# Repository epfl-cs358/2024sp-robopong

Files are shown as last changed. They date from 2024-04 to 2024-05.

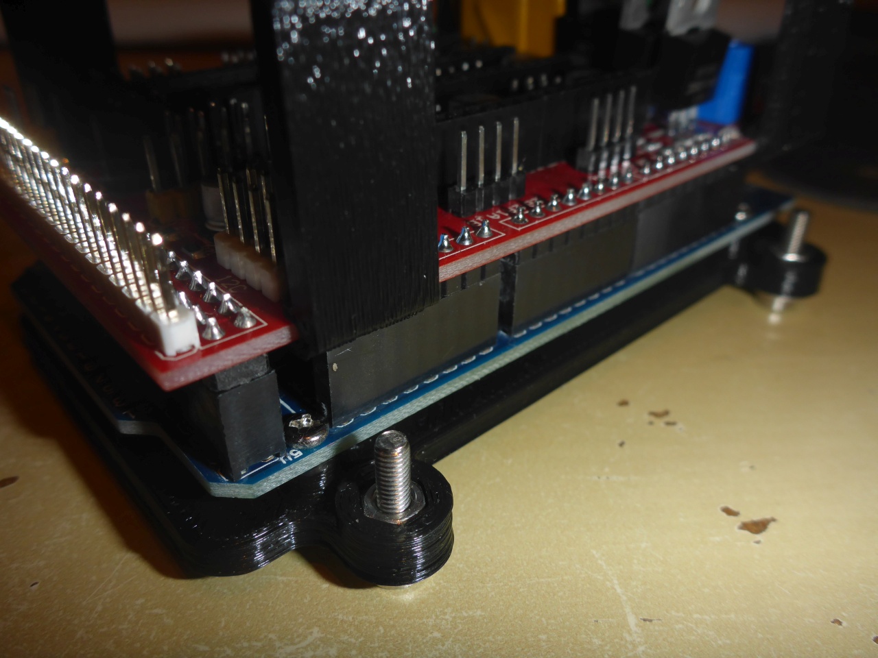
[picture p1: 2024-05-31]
cad/periphery/mega mount/images/P1020768.JPG

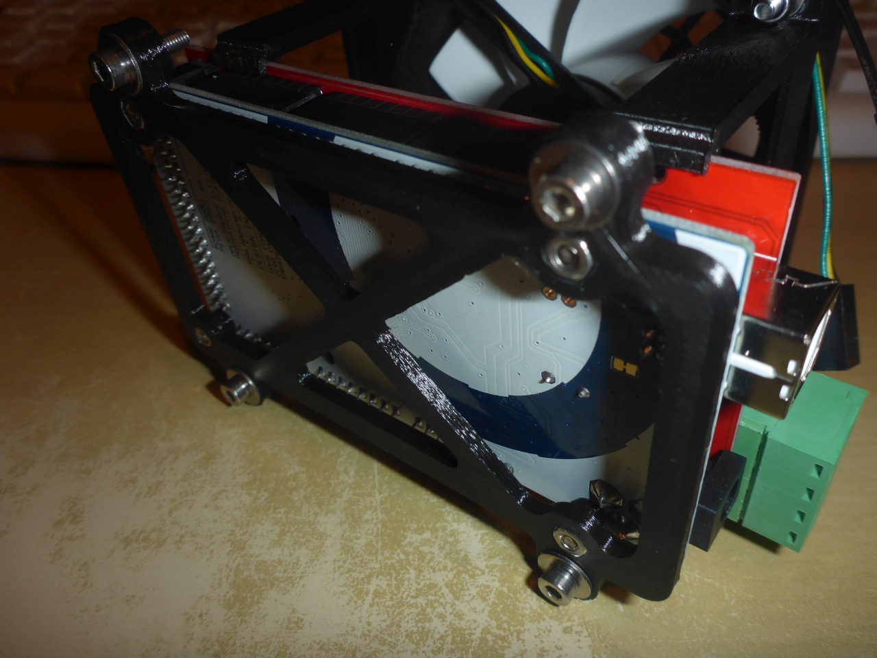
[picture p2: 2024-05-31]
cad/periphery/mega mount/images/P1020765.JPG

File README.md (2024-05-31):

## Robopong

The core concept of our project is a physical version of the classic Pong arcade game, where users bounce a ball back and forth with paddles while attempting to score goals by hitting the ball past the opposing player's paddle. Along with the regular two-player mode, we integrated computer vision into our project, providing the option of single player against a computer opponent, or a completely automated game.





### Authors
- [Amene Gafsi](https://github.com/Amene-Gafsi)
- [Connor Grant](https://github.com/cgrant0)
- [Célien Müller](https://github.com/cemuelle)
- [Jonathan Shu](https://github.com/jonathanshu87)
- [Andrew Yatzkan](https://github.com/AndrewYatzkan)

## BOM
- 2x b-g431b-esc1 motor driver
- 2x br3536 1200kv brushless motor
- 2x AS5600 magnetic encoder
- Arduino Mega
- 12V power supply
- 2x slide potentiometers
- LCD 16x2 screen
- I2C converter
- Webcam Logitech C270
- 2x buttons with LED
- 2x bearings for supporting the motor
- 4x linear bearings
- 4x 8mm by 40cm metal rails
- Belt
- MDF
- Velcro
- Metal rod for camera

## Wiring
### Motors drivers
#### Encoder
326759916-8e4414b6-f468-42d3-b0b5-9535e6a64daa [Schematic from](https://hackaday.io/project/177578-b-g431b-esc-brushless-servo-controller/log/190978-encoders)

To connect the AS5600 encoder to the B-G431B-ESC1 motor drivers, we need to make the following connection :

         +--------------------+       +----------------------+
         |  B-G431B-ESC1      |       |      AS5600          |
         |                    |       |                      |
         |     Z (SCL)     <--+-------+--> SCL               |
         |     B (SDA)     <--+-------+--> SDA               |
         |          5V     <--+-------+--> VCC               |
         |         GND     <--+-------+--> GND               |
         +--------------------+       +----------------------+
The pins on the AS5600 are well labeled
#### Arduino
To control the driver with an Arduino with Serial, we will need to use the RX/TX ports. We will also connect GND in order to have a shared ground and on one of the two drivers will be connect the 5V to the VIN of the Arduino in order to power the arduino.
326795159-361b4c3e-4f68-4188-b18f-7fbf75081d51 [Schematic from](https://www.st.com/resource/en/user_manual/um2516-electronic-speed-controller-discovery-kit-for-drones-with-stm32g431cb-stmicroelectronics.pdf)

         +--------------------+       +----------------------+
         |  B-G431B-ESC1      |       |     Arduino          |
         |  motor 0           |       |                      | 
         |                    |       |                      |
         |          GND    <--+-------+--> GND               |
         |           5V    <--+-------+--> 5V                |
         |           TX    <--+-------+--> RX (Pin 8)        |
         |           RX    <--+-------+--> TX (Pin 9)        |
         +--------------------+       +----------------------+

         +--------------------+       +----------------------+
         |  B-G431B-ESC1      |       |     Arduino          |
         |  motor 1           |       |                      | 
         |                    |       |                      |
         |          GND    <--+-------+--> GND               |
         |           TX    <--+-------+--> RX (Pin 10)       |
         |           RX    <--+-------+--> TX (Pin 11)       |
         +--------------------+       +----------------------+
#### Power and motor
326795266-6a96b532-8359-4901-882d-a318c4af6d5f [Schematic from](https://www.st.com/resource/en/user_manual/um2516-electronic-speed-controller-discovery-kit-for-drones-with-stm32g431cb-stmicroelectronics.pdf)
To power the drivers, we connect respectively the V- and the V+ to the ground and the 12V of our powersupply.
In our system, we are using some XT-60 connectors, on this connectors the flat side is the ground and the other with a sort of triangle is the +. Additionnaly we connect the female side to the power source.
To be able to connect a single power source to the two motor drivers, we make a Y cable.

To connect the motor to the driver, we solder 3 cables to the 3 big pads on the OUTPUT side.

### Potentiometers
To control the motors manually, we need to connect two potentiometers to the Arduino. Both potentiometers send output through the analog pins. We use the following connection (the potentiometer pins are labeled 1-3):

         +------------------------+       +----------------------+
         |  Slide potentiometer 0 |       |       Arduino        |
         |                        |       |                      | 
         |                        |       |                      |
         |          1          <--+-------+-->      GND          |
         |          2          <--+-------+-->      A0           |
         |          3          <--+-------+-->      5V           |
         +------------------------+       +----------------------+

         +------------------------+       +----------------------+
         |  Slide potentiometer 1 |       |       Arduino        |
         |                        |       |                      | 
         |                        |       |                      |
         |          1          <--+-------+-->      GND          |
         |          2          <--+-------+-->      A1           |
         |          3          <--+-------+-->      5V           |
         +------------------------+       +----------------------+

### Buttons and screen
To allow the users to progress through the game flow, we need to connect two buttons (with corresponding LEDs) and an LCD screen. Both + and NC for the LED and button respectively utilize the digital pins. We use the following connections:

         +---------------------+       +----------------------+
         |       Button 0      |       |       Arduino        |
         |   (next/player 0)   |       |                      | 
         |                     |       |                      |
         |     - (LED)      <--+-------+-->      GND          |
         |     GND (BUTTON) <--+-------+-->      GND          |
         |     + (LED)      <--+-------+-->      12           |
         |     NC (BUTTON)  <--+-------+-->      6            |
         +---------------------+       +----------------------+

         +---------------------+       +----------------------+
         |      Button 1       |       |       Arduino        |
         |   (enter/player 1)  |       |                      | 
         |                     |       |                      |
         |     - (LED)      <--+-------+-->      GND          |
         |     GND (BUTTON) <--+-------+-->      GND          |
         |     + (LED)      <--+-------+-->      13           |
         |     NC (BUTTON)  <--+-------+-->      7            |
         +---------------------+       +----------------------+

For the screen, we first solder the I2C converter to the back of the LCD screen, making sure the labeled 16 pins on the converter align with the correspondingly labeled holes on the screen. Then, we use the following connections:

         +---------------------+       +----------------------+
         |    I2C converter    |       |       Arduino        |
         |                     |       |                      | 
         |                     |       |                      |
         |         GND      <--+-------+-->      GND          |
         |         VCC      <--+-------+-->      5V           |
         |         SDA      <--+-------+-->      SDA          |
         |         SCL      <--+-------+-->      SCL          |
         +---------------------+       +----------------------+

To make wiring easier, we chose to use a shield board.

5acc8154-722d-4b54-9d1e-df4f039b3db4
bfca6097-a0ba-450b-9a1a-296cc2c2c26b

## General Assembly
First, laser cut and 3D print the necessary parts.
To laser cut for the [main box](https://github.com/epfl-cs358/2024sp-robopong/tree/main/cad/full%20box):
- Box walls
- Game board (from black plexiglass)
  
To 3D print for the [main box](https://github.com/epfl-cs358/2024sp-robopong/tree/main/cad/full%20box):
- 2x paddle-belt-rail attachment system
         - paddle load bearing mount
         - paddle (ensure top of paddle is red, everything else is black)
         - 2x belt attachments
- Gutter system
         - 2x long gutter
         - 2x middle gutter
         - 2x short gutter
         - 1x output  gutter
- Collection bowl
- 6x [wall liner in black TPU](https://github.com/epfl-cs358/2024sp-robopong/blob/main/cad/periphery/bouncy_wall_liner.3mf)
- 2x belt bearing
- 2x motor encoder case
- 2x backing plates for buttons
- 2x motor reduction gears
- 2x magnet case
- 2x rail to box mounts
- Arduino Mega mount
- Power supply mount
- C270 camera mount
- Screen mount

To laser cut for each [potentiometer](https://github.com/epfl-cs358/2024sp-robopong/tree/main/cad/joystick):
- Joystick case walls

To 3D print for each [potentiometer](https://github.com/epfl-cs358/2024sp-robopong/tree/main/cad/joystick):
- 2x linear rails
- Joystick slider
- Bottom half of joystick handle
- Top half of joystick handle

First, assemble the game board shell using the laser cut walls as shown in the 3D model (exploded view in [cad/README.md](https://github.com/epfl-cs358/2024sp-robopong/tree/main/cad)). Leave the outermost walls on the left and right side to attach after motor assembly. 

### Motor system assembly
To assemble the motor and belt system, first construct the motor reduction gear by cutting an appropriate length of belt and gluing it into the groove in the gear, effectively adding teeth to the gear. Screw this gear on to the motor, followed by the magnet case with the magnet in it (this should be glued in place)

b9bc51b0-cb36-4b83-855d-d3c8be783bce 2

Place the motor bearing and encoder in the 3D printed motor encoder holder as such:

2c66997f-9335-4c96-b54d-4510f0bba696
60660e97-f302-4b62-bc28-e89910602a5d 2

Then place the motor encoder holder on top of the magnet with encoder facing up to give the completed motor assembly:

fbca97d7-b42d-43a9-8b6f-95b957662d91

The motor can then be screwed into the base of the game board using the corresponding screw holes. Then, insert linear bearings into the appropriate clasps on each paddle mount print. Use screws (four per paddle mount) to tighten the linear rail clasps. 



Screw the belt attachments onto the paddle mount and attach the belt to one end by first placing a nut into the hexagonal indent on the belt attachment



pinching the belt into the notch, and turning a screw down the center. 



To insert the rails, first screw the rail-to-box mount into the side of the box with the corresponding screw holes. Push both rails through the rail/box mount attached to the box wall and clamp with screws.



Continue pushing the rails through the paddle mount with linear bearings and the corresponding rail holes on the opposite side of the game board. Loop the belt around the motor reduction gear and opposing belt bearing and attach the other end of the belt to the paddle mount with the belt attachment similar to before. 



The paddle mount should now be connected to the motor via the belt and should slide along the rails. Repeat on the other side. Then, wire the encoders and microcontrollers to the Arduino as shown above.

### Game board assembly
To assemble the game board, first sand the plexiglass to prevent glare from interfering with the computer vision. Then, run the ARUCO marker generation script (`scripts/gen_aruco.py`) and print the four markers. Attach these to the sanded game board, making sure that the detected corners align with the corners of the game board. 



Attach velcro strips along the back and front walls of the game board as well as the TPU wall linings. Ensure that the furry side of a velcro strip is attached on the back wall of the game board as this will ensure that the game board is able to be removed to access electronics.



### Gutters
Glue the gutter system together as shown in the 3D model. Insert the entire gutter system into the game box.



### Peripherals
Both buttons come with a plastic "nut" that holds the button together as seen here:



On the front of the board, unscrew the nut on each button and insert the button through the hole in the front of the box. On the inside wall, place the button backing plate and screw the plastic nut back on. The button's nut should now be compressing both the backing plate and the frontmost panel of the game box, securing the buttons in place.



Additionally, screw the screen into the screen mount and attach to the top of the game board. Wire the screen and both buttons as mentioned above. 

To construct the joysticks, first assemble the laser cut finger joint box. Then, snap the bottom half of the joystick onto the slider.



The top half of the joystick can then be glued on, forming the complete handle.



On the top plate, screw in both rails leaving one screw undone. Insert the slider between the rails, and secure the final screw. 





Then, attach the potentiometer to the joystick and screw the potentiometer into the top plate. Feed the potentiometer wires through the hole in the back of the box, and connect to the Arduino as mentioned above. 

For the camera, first insert the metal rod through the corresponding holes on the rear upper panel and bottom panel of the game box.



Attach the camera to the printed hinge mount and push this mount onto the top of the metal rod. Secure the rod in place.

Once all wiring is complete, attach the Arduino Mega to its mount and secure the mount to the bottom of the board. Place the power supply brick in its mount and secure to the bottom of the board as well. Glue the gutter system together and fit it along the inside walls of the game box and attach the collection bowl to the front of the box. The game board can now be inserted, the wall linings attached, paddles clipped in, and the product is ready to play. 

## Software
To run the project, we have to upload the [gameplay code](https://github.com/epfl-cs358/2024sp-robopong/blob/main/gameplay/gameplay.ino) to the arduino Mega board, the [driver code](https://github.com/epfl-cs358/2024sp-robopong/blob/main/simpleFOC/closed_loop-B_G431B_ESC1_AS5600/closed_loop-B_G431B_ESC1_AS5600.ino) to the two drivers (making sure to have the delay set at the beginning of the setup for one, but not the other driver in order to reduce the current peak during setup) and the [computer vision code](https://github.com/epfl-cs358/2024sp-robopong/blob/main/computer_vision/Computer_Vision.py) that run on a computer.

## Game and Computer Vision

To play the game, we must first launch the Python computer vision code. The Arduino should be connected to the laptop, and the port used should be specified in the first line of the main method. The camera must be connected to any USB port on the laptop.

Once the code is launched, it starts by calibrating the camera: it first detects the four Aruco Markers and then computes the transformation matrix for the frame. Next, motor calibration takes place by detecting the red triangular-shaped paddles. The system sends "Go UP" and "Go DOWN" commands to the Arduino through the serial port. Once the boundaries are reached, a stop command is sent to the Arduino. This step is crucial to establish concrete bounds of the board and to save the zero and maximum positions of each motor.

After reaching all four edges of the board, the code enters the main infinite loop of our algorithm. It detects the blue ball and red paddles by color detection, predicts the trajectory of the ball, and then sends the motors to the correct positions at the right time to hit the ball in computer player mode. Concurrently, the algorithm checks if a goal has occurred by performing the following checks:

If the ball is close enough to an edge, moving toward it, and then it is not visible for three consecutive frames, it is considered a goal.
In the event of a goal, a "goal 0" or "goal 1" command is sent to the Arduino depending on which player scored.

To exit the algorithm, press the 'q' button.

CV

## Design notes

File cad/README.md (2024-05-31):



Exploded view of `full_box.f3z` box structure assembly

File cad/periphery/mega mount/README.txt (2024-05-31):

Arduino Mega Ramps Frame / Bracket / Mount by GofX on Thingiverse: https://www.thingiverse.com/thing:2219359

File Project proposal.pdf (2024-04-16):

CS-358 - Robopong
Jonathan Shu, Amene Gafsi, Andrew Yatzkan, Connor Grant, Célien Muller Team project proposal revision : Robopong

The core concept of our proposal is to design and construct a box that houses an electronic version of the classic Pong game. On the top of this box, the Pong game will be played, while the internal space will contain all the necessary electronics. The game involves a ball moving back and forth between two players. The primary goal is to 'hit' the ball with a paddle, preventing it from passing by. For each paddle, we can either choose to be controlled by a human part or managed automatically by a robot that tracks the ball in real time.

Detailed construction instructions for a manual version of the game can be found on the Evil Mad Scientist website at https://www.evilmadscientist.com/2010/a-playable-game-of-tabletop-pong/ . Additionally, a demonstration of the game in action is available in a video on YouTube, which can be viewed at https://www.youtube.com/watch?v=Z5mjx1iYt5g&t=67s. However, our project significantly diverges from this manual model since we plan to integrate automation into the game to control the robotic components and manage the score (details below). This addition will transform the traditional manual gameplay into an interactive and technologically advanced experience, blending classic entertainment with modern engineering.

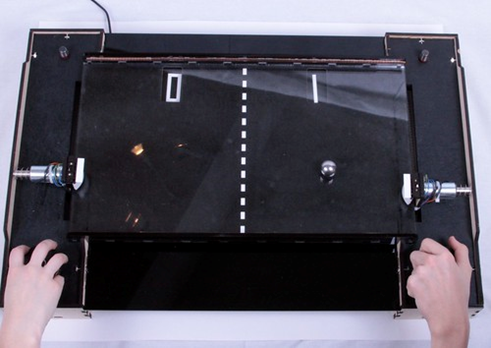
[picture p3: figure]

Pong Game: A Realistic Representation of the Classic Game

Technical Overview :
Mechanical assembly: Box design, size, joints, camera mount
The play area will measure 35 cm x 50 cm and will rest on top of the game box with faces measuring 55 cm x 90 cm and a height of 10 cm. The faces of the box will be laser cut and connected via comb joints, allowing for easy removal to access internal electronics. The play area will have a slightly elevated center to prevent the ball from getting stuck in the middle during gameplay. There will be a camera mounted above the game board for computer vision purposes. On each player side, there will be a platform extending 10 cm from the game box that the slide potentiometers will be mounted upon. At the top of the game board we will have a small OLED screen that will display the score, handle the starting and ending of games, and allow users to switch between various game modes (levels of automation).
To keep a constant flow of gameplay, we will include two gutters on each “player” side behind each paddle. If the ball lands in the gutter, it will roll underneath the board, trigger a limit switch, and be brought back up by a tile that first lowers to pick it up. The tile will have a small divot in it to keep the ball from rolling out and present it directly in front of the paddle to be hit. The side that has been scored upon gets the small advantage of being able to “serve” the ball on the next round. As a preliminary goal, we will direct the ball to an opening at the front of the game board for a person to manually place and start the next round.

Computer vision: Software, color coordination, transforms, algorithm
The game features an option for robotic opponents To achieve this, we will employ a camera positioned atop the gaming surface taking in real time footage of gameplay. We plan to color our play area black while the ball, paddles, and calibration spots (one per corner of the play area) will each have their own unique colors. Using color detection, we will be able to detect the calibration spots, ball, and paddles. With the calibration spots, we will apply a transform to “flatten” the game board image and construct a representation of it. Our algorithm will then provide precise real-time coordinates and trajectory predictions for the ball, allowing us to make properly timed hits with the paddles. It's important to note that all computations for the computer vision algorithm will be executed locally, without reliance on internet sockets. This design choice ensures minimal latency, enhancing the gaming experience.

Motor System: Brushless motors, encoding, rails, mounts, belts
Once the trajectory is predicted, the robotic paddle is activated. Controlled with a belt system, the movement of the paddle will be driven by a brushless motor used in conjunction with the SimpleFOC library. The paddle itself will be attached to linear ball bearings that slide on 8 mm rails extending the length of each player side.

Paddle System: Connection to rail mount, size, shape, actuation vs no actuation On the sides closest to each player, we will have a robotic paddle 3D printed into a wedge shape measuring 7 cm wide at the base. When the ball contacts the paddle, the wedge shape will ensure that the direction of the paddle’s movement (parallel to the “player” side) will also partially propel the ball forward to the opposite player. The paddle will be 3D printed in two parts: a backing that remains attached to the linear ball bearings and a detachable wedge.
For detecting whether a goal has been scored, we have several options. Programmatically, we could use our computer vision algorithm to detect when the ball has passed a certain threshold or can no longer be detected (is in the gutter). Physically, we could also position a limit switch inside the gutter that is pressed when the ball enters, or use our photogate to infer that a goal has been scored (two gate crossings implies the ball has been hit back while one implies a goal).

Electronic components: Slide pots, microcontrollers, power system, cabled connections
We will also provide the option for manual play as well. Paddles on both sides of the board will be able to be controlled by slide potentiometers mounted outside the play area. The relative position of the slide potentiometer will be scaled to the length of a “player” side and used to determine where the motor should position the paddle on the actual game board.
Each slide potentiometer will be plugged into a corresponding Nucleo 64 board. Meanwhile, in the case of automated ball return, the two required stepper motors will be controlled via an Arduino Uno. The physical scoring detection system and screen output will also be controlled with the Arduino Uno. Our motors will be powered at 12V or 24V if we get permissions to allow a faster movement, while the two Nucleo 64 boards, Arduino Uno, and camera will be powered from a computer if we need data, otherwise we will use a step down converter to adjust the main power supply to the desired 5V voltage.

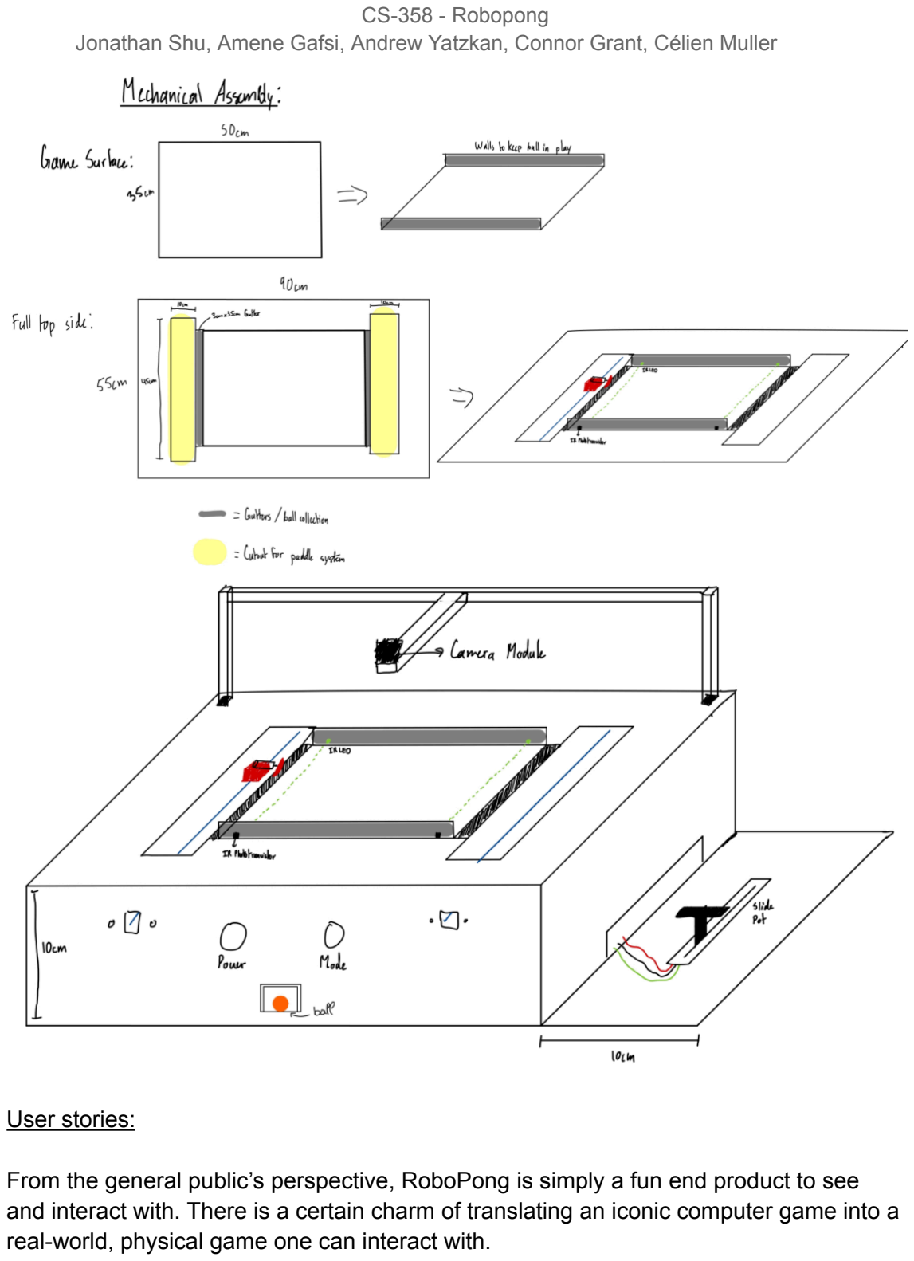
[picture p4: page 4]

User stories:

From the general public’s perspective, RoboPong is simply a fun end product to see and interact with. There is a certain charm of translating an iconic computer game into a real-world, physical game one can interact with.

From our group’s perspective, one major reason we all chose to work on RoboPong was because we also felt the end result would be a fun and interesting product to play with. This project also comes with many interesting engineering problems to solve, which we thought would be challenging and fulfilling for this class.

From the perspective of the professor, a large portion of making our project function is low-latency computer vision for ball detection and position prediction for automated play. This part of our project is applicable to future projects that require computer vision for similarly fast-paced or responsive purposes.

From an IC public relations perspective, this project would make a good demo. It is instantly recognizable and associated with childhood fun and nostalgia. As mentioned earlier, there is an element of uniqueness in making a physical version of a virtual game. The demo would also be able to involve audience members, allowing them to actually play physical Pong and experience the project. In addition, the project is suitably complex both in build and software, providing a good demo of the possibilities of the IC department.

Future Opportunities ?

Looking ahead, our project presents promising prospects for future endeavors. It could lay the groundwork for a startup venture, focusing on developing robotic opponents for traditional manual games. This innovative approach would inject a contemporary edge into classic entertainment, appealing to a wide audience.

Furthermore, there's potential to commercialize our unique version of the Pong game. By offering a fully built Pong game with integrated automation features, we could cater to gaming enthusiasts and tech-savvy consumers seeking a distinctive gaming experience. This opens doors to acquiring users beyond EPFL, potentially reaching a broader market and establishing our product as a staple in modern gaming.

Risk Assessment :

Considering there are many moving parts and sensors within this build, there are a few apparent risks to be assessed. First would be with the robotic paddle actuation system. The primary areas of concern are the interaction point between the solenoid and the paddle, the stability of the solenoid-paddle system, and the time between hits. The best way to mitigate these risks is to conduct tests on various paddle prototypes prior to assembling the final system. Different paddle sizes and shapes can be 3D printed, and there can be various connective system prototypes that can be tried and tested: a hinge system, a physical connection to the solenoid, or a stationary solenoid that moves a mechanical system.
Continuing with the paddle system and its related components, the laser gate system that triggers solenoid actuation will need to be tuned. It’s possible there will be some delay, so triggering actuation may not be on time. Additionally, the system must be fault tolerant, such that actuation does not occur at inopportune times. The railing systems must be tested at various speeds and the limit switches must be placed properly to avoid system damage. Some steps to complete this are to test the solenoid pusher under various operating conditions to assess reliability and consistency. Next we can implement fail-safe mechanisms to detect and address malfunctions or misfires promptly. Finally, we’ll incorporate robust mechanical design principles to ensure durability and longevity of the solenoid mechanism.
The real-time computer vision system is a large risk area for us. Developing a streamlined computer vision algorithm capable of accurately tracking the ball in real-time may prove challenging, particularly considering variations in lighting conditions and ball movement speeds. To start, we can allocate sufficient time for algorithm development and testing, considering potential complexities. When testing the camera system separate from the actuators and game field, we can implement error handling mechanisms and discover any potential environmental factors. We may consider integrating machine learning techniques to enhance the algorithm's adaptability and performance.
Our system plan relies on two identical subsystems working in parallel. Controlling two systems in parallel may present some significant challenges, both when it comes to power delivery and communication. There are a variety of communication methods across the planned system, so we’ll test each individually (serial, usb-usb, camera-computer, etc), then slowly integrate each component one at a time. The subsystems can be mapped online so the communication pathways can be optimized. Ensuring seamless integration of manual and automated gameplay modes, as well as implementing features such as ball retrieval and scoring mechanisms, may pose challenges in terms of system complexity and user interaction.
We can conduct user testing and feedback sessions to iteratively refine gameplay mechanics and user interface design. Another solution is to prioritize simplicity and intuitiveness in system operation, providing clear instructions and visual cues to guide players. We’ll continuously monitor user feedback and iterate on system features to enhance overall gameplay experience.

The Bill of Materials :

Name | Shop | Qte | Price (CHF) | Total price (CHF)
8mm rails | CS-358 | 2 | x | x
Linear ball bearings | CS-358 | 2 | 0 | 0
17HS4401 | CS-358 | 2 | 15 | 30
L298N (driver) | CS-358 | 2 | 5 | 10
Encoder | CS-358 | 2 | x | x
28BYJ-48 + ULN2003 | CS-358 | 2 | 2 | 4
Belt | CS-358 | 2*1m | x | x
Nucleo 64 | CS-358 | 2 | x | x
Arduino Uno | CS-358 | 1 | 5 | 5
Webcam logitech C270 | https://www.conrad.ch/fr/p/webcam-hd-1280-x-720-pixel-logitech-c270-pied-de -support-support-a-pince-1426807.html (https://www.conrad.ch/fr/p/webcam-hd-1280-x-720-pixel-logitech-c270-pied-de-support-support-a-pince-1426807.html) | 1 | 15,95 | 15,95
Slide potentiometer | https://www.reichelt.com/ch/fr/potentio m-tre-glissi-re-alps-de-grande-qualit-lin -aire-st-r-rsa0n12-lin10k-p73873.html (https://www.reichelt.com/ch/fr/potentiom-tre-glissi-re-alps-de-grande-qualit-lin-aire-st-r-rsa0n12-lin10k-p73873.html) | 2 | 5.11 | 10.22
Power Supply | https://www.reichelt.com/ch/fr/bloc-d-ali mentation-de-table-78-w-12-v-6-5-a-vt-3240-p215629.html (https://www.reichelt.com/ch/fr/bloc-d-alimentation-de-table-78-w-12-v-6-5-a-vt-3240-p215629.html) | 1 | 19,02 | 19,02
Power supply plug | https://www.distrelec.ch/fr/jack-de-puis sance-prise-femelle-angle-droit-x6-3xm m-cliff-fc681465/p/14205870 (https://www.distrelec.ch/fr/jack-de-puissance-prise-femelle-angle-droit-x6-3xmm-cliff-fc681465/p/14205870) | 1 | 2.27 | 2.27
Step down converter | https://www.reichelt.com/ch/fr/cartes-d e-d-veloppement-r-gulateur-de-tension -20-w-convertiss-debo-dcdc-20w-p233 018.html (https://www.reichelt.com/ch/fr/cartes-de-d-veloppement-r-gulateur-de-tension-20-w-convertiss-debo-dcdc-20w-p233018.html) | 1 | 4,70 | 4,70

Limit switch | https://www.distrelec.ch/fr/microrupteur
-csm405-5a-1co-25n-levier-rouleaux-si mule-camdenboss-csm40540f/p/13570 363 (https://www.distrelec.ch/fr/microrupteur-csm405-5a-1co-25n-levier-rouleaux-simule-camdenboss-csm40540f/p/13570363)
8 | 0.768 | 6.15
Set of balls | https://www.galaxus.ch/fr/s5/product/no name-jeu-de-billes-8-pcs-en-filet-ass-ci rcuit-de-billes-14615761 (https://www.galaxus.ch/fr/s5/product/noname-jeu-de-billes-8-pcs-en-filet-ass-circuit-de-billes-14615761)
| https://www.galaxus.ch/fr/s15/product/k arlie-balles-de-caoutchouc-mousse-bal les-jouets-pour-chien-12543724 (https://www.galaxus.ch/fr/s15/product/karlie-balles-de-caoutchouc-mousse-balles-jouets-pour-chien-12543724)
| https://www.galaxus.ch/fr/s15/product/k arlie-balle-en-caoutchouc-plein-balles-j ouets-pour-chat-12543498 (https://www.galaxus.ch/fr/s15/product/karlie-balle-en-caoutchouc-plein-balles-jouets-pour-chat-12543498)

1

1

1

4.90

3.05

2.90

4,9

3.05

2,90

119,20
The price below are from the 31.03.2024

Initial Design: ~1.03m^2 of 5mm MDF = 9,27chf 8mm bar

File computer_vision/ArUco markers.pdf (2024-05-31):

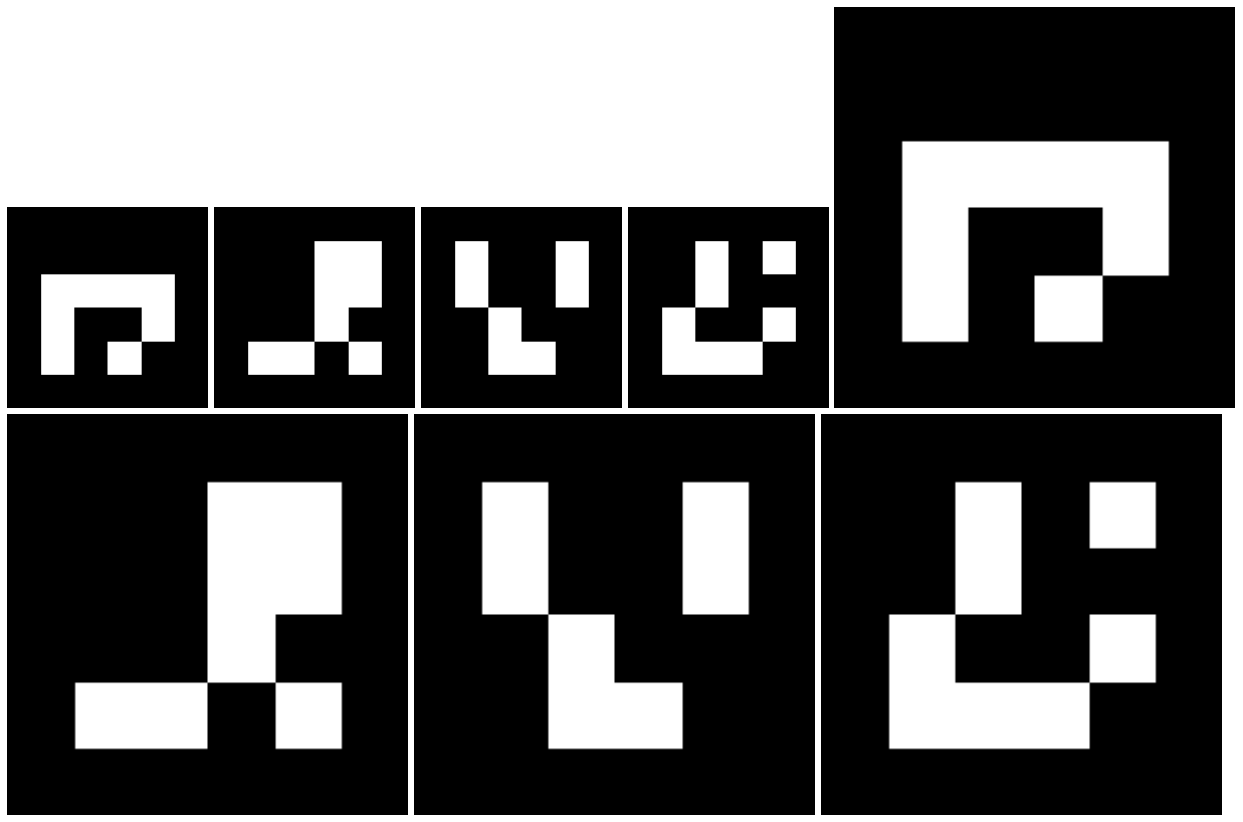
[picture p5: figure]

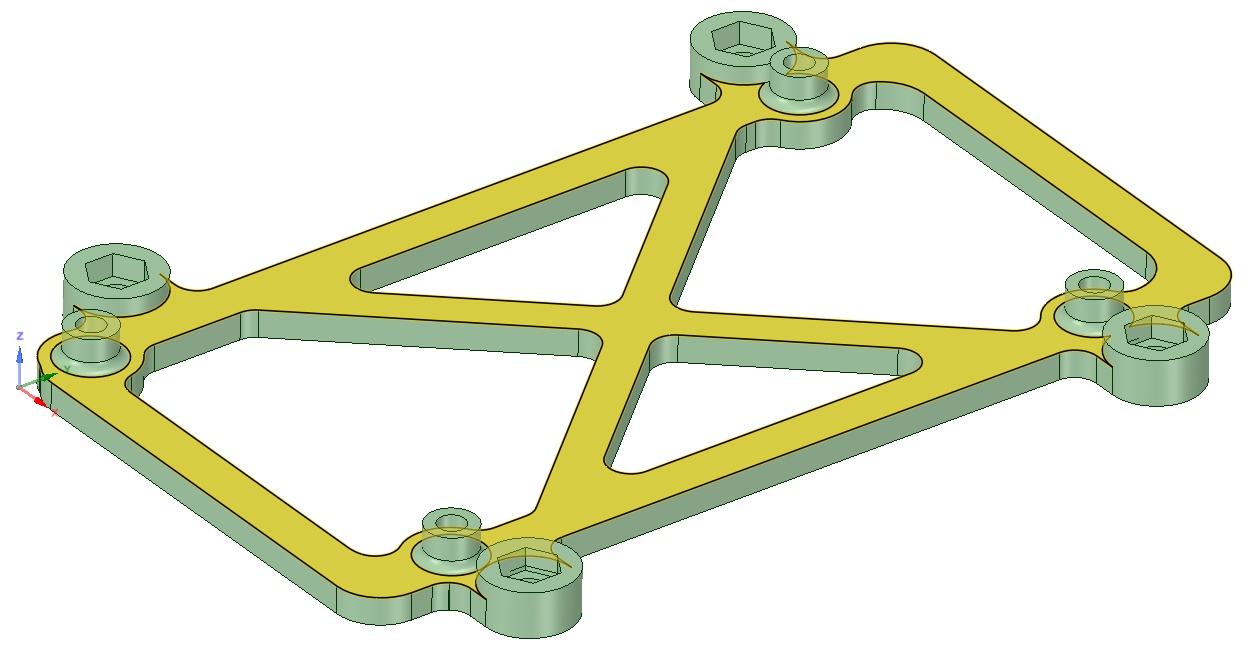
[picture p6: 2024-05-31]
cad/periphery/mega mount/images/MegaRampsFrame.jpg

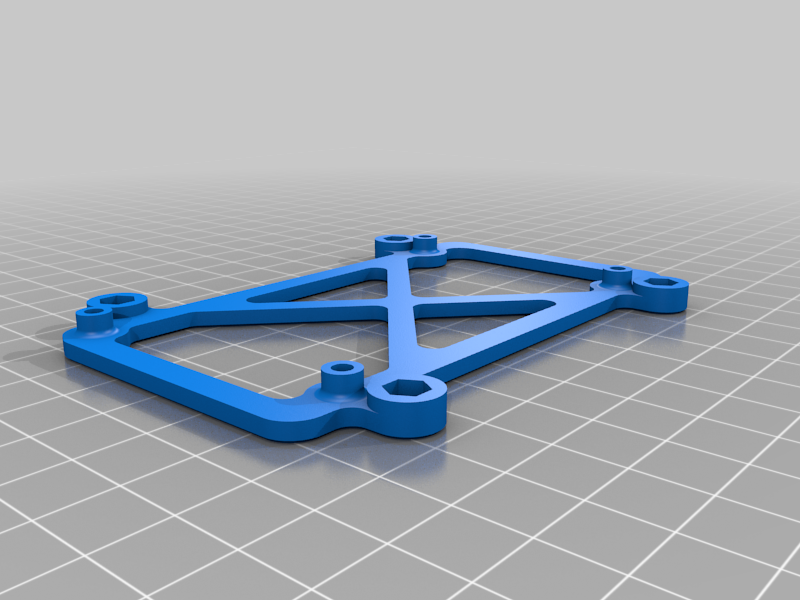
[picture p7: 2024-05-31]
cad/periphery/mega mount/images/7abde0f5339573b9ac54fe0878a5589d.png

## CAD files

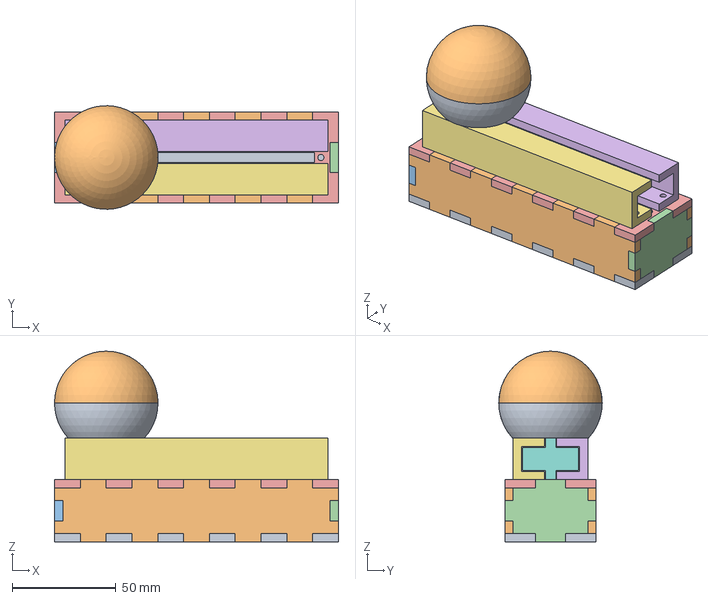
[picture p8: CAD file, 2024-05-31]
cad/joystick/joystick.step
137.0 x 50.0 x 92.0 mm

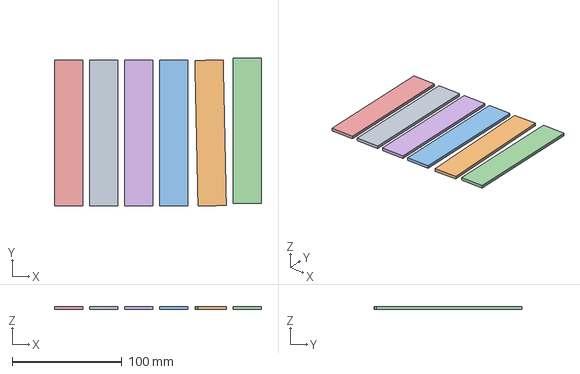
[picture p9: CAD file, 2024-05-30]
cad/periphery/bouncy_wall_liner.3mf
189.0 x 135.4 x 3.00 mm
Shape-Box x 6

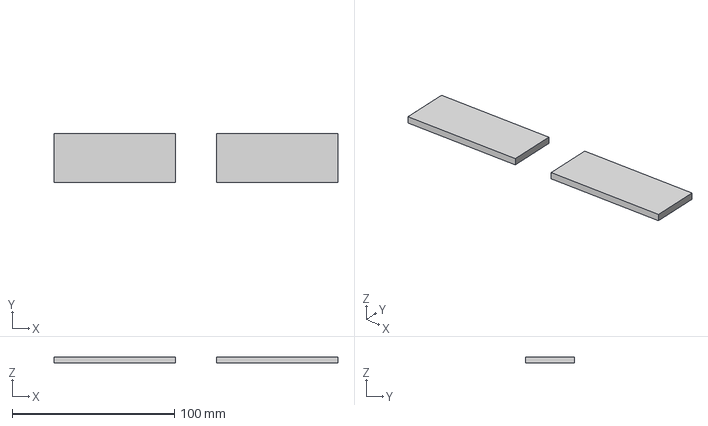
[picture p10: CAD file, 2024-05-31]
cad/periphery/button plates/button_nameplates.step
175.0 x 30.1 x 4.00 mm

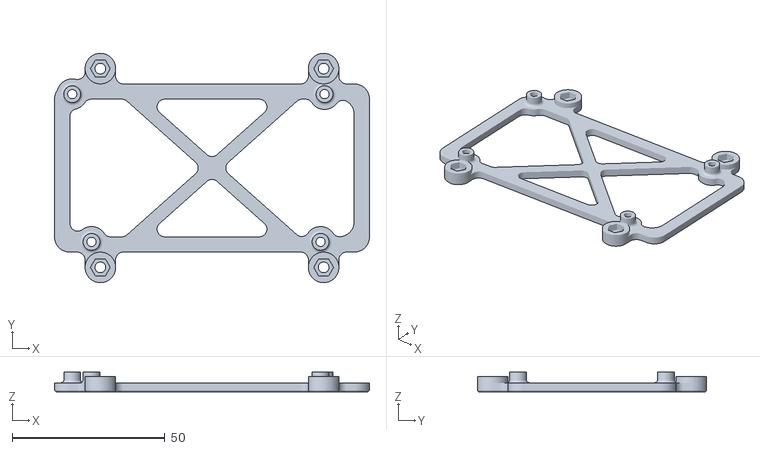
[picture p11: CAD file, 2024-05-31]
cad/periphery/mega mount/files/mega_mount.stl
103.0 x 75.0 x 6.50

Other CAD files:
cad/joystick/joystick.f3d
cad/periphery/button plates/button_nameplates.f3d

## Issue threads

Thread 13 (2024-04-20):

[CV] Prototype of ball motion prediction

AndrewYatzkan, 2024-04-20:
Won't be a perfectly elastic collision. May need to collect data and train a model to get accurate predictions.

Closed 2024-06-01.

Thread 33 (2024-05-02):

Send correct final position and speed to the arduino

Amene-Gafsi, 2024-05-02:
send final, correct position and speed to motors based on the prediction of the CV

Closed 2024-06-01.

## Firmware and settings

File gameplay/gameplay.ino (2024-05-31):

#include <ezButton.h>
#include <LCD_I2C.h>
#include <SoftwareSerial.h>

#define LED_PIN_1 13
#define LED_PIN_2 12

#define STEP_INCREMENT 0.05  // Initial radian increment for searching limits

SoftwareSerial serialMotor0(8, 9); // RX, TX
SoftwareSerial serialMotor1(10, 11);

float minLimitM0 = -15.0;
float maxLimitM0 = 15.0;

float minLimitM1 = -15.0;
float maxLimitM1 = 15.0;

long last = 0;

LCD_I2C lcd(0x3F, 16, 2); // address can change, check wiring on github issue for connecting screen
ezButton button1(7);  // next or player 1
ezButton button2(6); // enter or player 2

int curr;
String states[] = {"automated", "single player", "two player"};
bool modeSelected = false;
bool player1Ready = false;
bool player2Ready = false;
bool gameEnd = false;
bool restart = false;
int lScore= 0;
int rScore = 0;
int computerID = 0;


void setup()
{
    lcd.begin(); 
    lcd.backlight();
    button1.setDebounceTime(50);
    button2.setDebounceTime(50);
    pinMode(LED_PIN_1, OUTPUT);
    digitalWrite(LED_PIN_1, LOW);
    pinMode(LED_PIN_2, OUTPUT);
    digitalWrite(LED_PIN_2, LOW);
    button1.setCountMode(COUNT_FALLING);
    Serial.begin(115200);
    serialMotor0.begin(115200);
    serialMotor1.begin(115200);

    last = millis();

    lcd.print("Waiting for");
    lcd.setCursor(0, 1);
    lcd.print("calibration");
    lcd.setCursor(0, 0);

    while (!Serial){
      ;
      //Implement a manual calibration
    }
    
    calibrateMotors();
    // lcd.clear();
}

int potentiometerValue0 = 0;
int potentiometerValue1 = 1;
int prevValue0 = 0;
int prevValue1 = 1;

void loop()
{
  button1.loop(); 
  button2.loop();

  // game mode selection
  if (!modeSelected) {
    curr = button1.getCount() % 3;
    lcd.print(states[curr]+"       ");
    lcd.setCursor(0, 0);
  } 


  if (button2.isPressed()) {
    modeSelected = true;
    lcd.print(states[curr]);
    lcd.setCursor(0,1);
    lcd.print("selected. Ready?");
  }

  // players confirm ready
  if (modeSelected) {
    if (curr == 0) {
      player2Ready = true;
      player1Ready = true;
    }
  }

  while (modeSelected && (!player1Ready || !player2Ready) ) {
    button1.loop();
    button2.loop();

    if (button1.isPressed()) {
      player1Ready = true;
      if (curr == 1) {
        player2Ready = true;
        computerID = 1;
      }
    } 
    if (player1Ready) {
      digitalWrite(LED_PIN_1, LOW);
    } else {
      digitalWrite(LED_PIN_1, HIGH);
    }
    if (button2.isPressed()) {
      player2Ready = true;
      if (curr == 1) {
        player1Ready = true;
        computerID = 0;
      }
    } 
    if (player2Ready) {
      digitalWrite(LED_PIN_2, LOW);
    } else {
      digitalWrite(LED_PIN_2, HIGH);
    }
  }
  
  // game countdown
  if (player1Ready && player2Ready) {
    for (int i = 3; i >= 1; i--) {
      lcd.clear();
      digitalWrite(LED_PIN_1, LOW);
      digitalWrite(LED_PIN_2, LOW);
      delay(750);
      lcd.print(String(i)+"...");
      digitalWrite(LED_PIN_1, HIGH);
      digitalWrite(LED_PIN_2, HIGH);
      delay(750);
    }
    lcd.clear();
    lcd.print(String(lScore) + "-" + String(rScore));
    digitalWrite(LED_PIN_1, LOW);
    digitalWrite(LED_PIN_2, LOW);
  }

  // gameplay
  while (player1Ready && player2Ready && lScore < 5 && rScore < 5) {
    String command_received = readCommand();
    if (curr == 2) {
      twoPlayer(command_received);
    } else if (curr == 1) {
      singlePlayer(command_received);
    } else {
      automated(command_received);
    }
    
  }
  
  // ending sequence
  if (lScore == 5) {
    gameEnd = true;
    lcd.setCursor(0,0);
    lcd.print("Player two wins");
    lcd.setCursor(0,1);
    lcd.print("Continue?");
    for (int i = 0; i <10; i++) {
        digitalWrite(LED_PIN_2, HIGH);
        delay(100);
        digitalWrite(LED_PIN_2, LOW);
        delay(100);
    }
  } else if (rScore == 5) {
    gameEnd = true;
    lcd.setCursor(0,0);
    lcd.print("Player one wins");
    lcd.setCursor(0,1);
    lcd.print("Continue?");
    for (int i = 0; i < 10; i++) {
      digitalWrite(LED_PIN_1, HIGH);
      delay(100);
      digitalWrite(LED_PIN_1, LOW);
      delay(100);
    }
  }

  while (gameEnd && !restart ) {
      button2.loop();
      if (button2.isPressed()) {
        restart = true;
      }
  }

  if (restart) {
    modeSelected = false;
    player1Ready = false;
    player2Ready = false;
    gameEnd = false;
    restart = false;
    lcd.clear();
    lScore = 0;
    rScore = 0;
    moveMotor(0, 512, 200);
    moveMotor(1, 512, 200);
  }
}

void twoPlayer(String command_received) {
  if(millis()-last > 10){
    potentiometerValue0 = analogRead(A1);
    potentiometerValue1 = analogRead(A0);

    if (abs(prevValue0 - potentiometerValue0) > 0){
      moveMotor(0, potentiometerValue0, 200);
    }
    delay(10);
    if (abs(prevValue1 - potentiometerValue1) > 0){
      moveMotor(1, potentiometerValue1, 200);
    }
  }
  checkGoal(command_received);
}

void singlePlayer(String command_received){
  checkGoal(command_received);

  if (command_received.startsWith("game ")){
    delay(20);
      int motor = command_received.substring(5,6).toInt();
      if (motor == computerID) {
        float command = command_received.substring(7).toFloat();
        moveMotor(motor, command, 200);
      }
  } else if(millis()-last > 10){
    if (computerID == 1) {
      potentiometerValue0 = analogRead(A1);
      if (abs(prevValue0 - potentiometerValue0) > 0){
        moveMotor(0, potentiometerValue0, 200);
      }
    } else {
      potentiometerValue1 = analogRead(A0);
      if (abs(prevValue1 - potentiometerValue1) > 0){
        moveMotor(1, potentiometerValue1, 200);
      }
    }
  }
}

void automated(String command_received) {
  if (command_received.startsWith("game ")){
      int motor = command_received.substring(5,6).toInt();
      float command = command_received.substring(7).toFloat();
      moveMotor(motor, command, 200);
  }
  checkGoal(command_received);
}
/*
 * id         : which motor we want to control, 0 or 1
 * position   : position between 0 and 100 that we want the motor to goes to 
 * speed      : speed in rad/s that we want to move
*/
void moveMotor(int id, float position, float speed){
  if (position < 0 || position >1023 || millis()-last < 10 ){
    return;
  }
  last=millis();

  if(id == 0){
    float range = maxLimitM0 - minLimitM0;
    float targetPosition = minLimitM0 + (position / 1023.0) * range;
    sendCommandToMotor(getMotorSerial(0), moveMotorCommand(targetPosition, speed));
  }
  if (id == 1){
    float range = maxLimitM1 - minLimitM1;
    float targetPosition = minLimitM1 + (position / 1023.0) * range;
    sendCommandToMotor(getMotorSerial(1), moveMotorCommand(targetPosition, speed));
  }
}

void SerialBridge(){
  if (Serial.available() > 0) {
    String input = Serial.readStringUntil('\n');
    
    serialMotor0.println(input);
  }

  if (serialMotor0.available() > 0) {
    String messageReceived = serialMotor0.readStringUntil('\n');
    
    Serial.print("Received: ");
    Serial.println(messageReceived);
  }
}

void checkGoal(String command_received) {
  if (command_received.startsWith("goal ")){
    int id = command_received.substring(5,6).toInt();
    if (id == 0) {
      rScore += 1;
      for (int i = 0; i < 5; i++) {
        digitalWrite(LED_PIN_1, HIGH);
        delay(100);
        digitalWrite(LED_PIN_1, LOW);
        delay(100);
      }
      lcd.setCursor(0,0);
      lcd.print(String(rScore));
    } else {
      lScore += 1;
      for (int i = 0; i < 5; i++) {
        digitalWrite(LED_PIN_2, HIGH);
        delay(100);
        digitalWrite(LED_PIN_2, LOW);
        delay(100);
      }
      lcd.setCursor(2,0);
      lcd.print(String(lScore));
    }
  }
}
SoftwareSerial getMotorSerial(int id){
  if(id == 0){
    return serialMotor0;
  }
  else if(id == 1){
    return serialMotor1;
  }
}

void sendCommandToMotor(SoftwareSerial serial, String command) {
  serial.println(command);
}

String moveMotorCommand(float position, float speed){
  String speedString = (speed == -1) ? "" : " " + String(speed, 2);
  return ("M" + String(position, 2) + speedString);
}

void playGame() {
  while (Serial.available() == 0) {}
  String side = Serial.readString();
  side.trim();
  Serial.println(side);
  if (side.equals("l")) {
    lScore += 1;
    for (int i = 0; i < 5; i++) {
      digitalWrite(LED_PIN_1, HIGH);
      delay(100);
      digitalWrite(LED_PIN_1, LOW);
      delay(100);
    }
    lcd.setCursor(0,0);
    lcd.print(String(lScore));
  } 
  if (side.equals("r")) {
    rScore += 1;
    for (int i = 0; i < 5; i++) {
      digitalWrite(LED_PIN_2, HIGH);
      delay(100);
      digitalWrite(LED_PIN_2, LOW);
      delay(100);
    }
    lcd.setCursor(2,0);
    lcd.print(String(rScore));
  }
}

void calibrateMotors(){
  bool m0Down = false;
  bool m0Up = false;
  bool m1Down = false;
  bool m1Up = false;
  String command_received = "";
  String command = "";
  int motor = -1;
  float position0 = 0;
  float position1 = 0;

  lcd.clear();
  lcd.print("Calibrating");
  lcd.setCursor(0, 1);
  lcd.print("motors");
  lcd.setCursor(0, 0);

  while(!(m0Down && m0Up && m1Down && m1Up)){
    command_received = readCommand();

    if (command_received.startsWith("cal ")){
      motor = command_received.substring(4, 5).toInt();
      command = command_received.substring(6);
    }
    float calibration_speed = 200;

    if(command.equals("up")){
      if (motor == 0) {
        position0 += STEP_INCREMENT;
        sendCommandToMotor(getMotorSerial(motor), moveMotorCommand(position0, calibration_speed));
      }
      else if (motor == 1) {
        position1 += STEP_INCREMENT;
        sendCommandToMotor(getMotorSerial(motor), moveMotorCommand(position1, calibration_speed));
      }
      command_received = "";
      command = "";
    }
    else if (command.equals("down")){
      if (motor == 0) {
        position0 -= STEP_INCREMENT;
        sendCommandToMotor(getMotorSerial(motor), moveMotorCommand(position0, calibration_speed));
      }
      else if (motor == 1) {
        position1 -= STEP_INCREMENT;
        sendCommandToMotor(getMotorSerial(motor), moveMotorCommand(position1, calibration_speed));
      }
      command_received = "";
      command = "";
    }
    else if (command.equals("done up")){
      if (motor == 0) {
        m0Up = true;
        maxLimitM0 = position0;
      }
      else if (motor == 1) {
        m1Up = true;
        maxLimitM1 = position1;
      }
      command_received = "";
      command = "";
    }
    else if (command.equals("done down")){
      if (motor == 0) {
        m0Down = true;
        minLimitM0 = position0;
      }
      else if (motor == 1) {
        m1Down = true;
        minLimitM1 = position1;
      }
      command_received = "";
      command = "";
    }
  }

  moveMotor(0, 512, 200);
  delay(10);
  moveMotor(1, 512, 200);
  lcd.clear();
}

String readCommand(){
  String command_received = "";
  if (Serial.available() > 0) {
      command_received = Serial.readStringUntil('\n');
      command_received.trim();
    }
    return command_received;
}

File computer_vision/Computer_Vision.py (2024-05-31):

from collections import deque
import cv2.aruco as aruco
import numpy as np
import imutils
import serial
import time
import cv2

# Constants
board_bottom_limit = 450
ball_radius_lower = 5
move_urgent_time = 0.35
paddle_min_area = 10
board_top_limit = 41

# Ball and paddle color ranges
redRange = [(160, 50, 50), (180, 255, 255)] # paddles
blueRange = [(40, 150, 200), (100, 255, 255)] # ball


paddle0_pts = deque(maxlen=64)
paddle1_pts = deque(maxlen=64)
ball_pts = deque(maxlen=64)
transformation_matrix = None
pixel_to_motor_coords = 0
position_sent = False
direction = -1
board_center = 0
goal_sent = False
width = 0
height = 0

def main():
    ser = serial.Serial('COM4', 115200)
    cap = cv2.VideoCapture(1, cv2.CAP_DSHOW) 
    frame = camera_on(cap)
    if frame is None:
        print("Problem with camera initialization.")
        return
    calibrate_camera(cap, ser)
    calibrate_paddles(cap, ser)
    track_ball_and_paddles(cap, ser)
    ser.close()
   
def camera_on(cap):
    global width, height, board_center, pixel_to_motor_coords
    time.sleep(2.0)
    if not cap.isOpened():
        return None
    ret, frame = cap.read()
    if not ret:
        return None
    height, width = frame.shape[:2]
    board_center = width // 2
    pixel_to_motor_coords = 1023 // height
    return frame

def calibrate_camera(cap, ser):
    motor0_moved = False
    motor1_moved = False
    time0 = 0
    time1 = 0
    check_again = 0

    global transformation_matrix
    # Define destination points (corners of the image)
    dst_points = np.float32([
        [0, 0],                # Upper-left corner
        [width - 1, 0],        # Upper-right corner
        [width - 1, height - 1],# Lower-right corner
        [0, height - 1]        # Lower-left corner
    ])

    # Last known positions of markers, indexed by their ID
    last_known_positions = {1: None, 2: None, 3: None, 4: None}
    aruco_dict = aruco.getPredefinedDictionary(cv2.aruco.DICT_4X4_50)
    while True:
        ret, frame = cap.read()
        if not ret:
            break
        gray = cv2.cvtColor(frame, cv2.COLOR_BGR2GRAY)
        corners, ids, _ = aruco.detectMarkers(gray, aruco_dict)
        aruco.drawDetectedMarkers(frame, corners, ids)
        if ids is not None:
            for id_array, corner in zip(ids, corners):
                id = id_array[0]
                if id in last_known_positions:
                    last_known_positions[id] = corner[0][0]
        
        if all(last_known_positions[id] is not None for id in last_known_positions):
            src_points = np.float32([
                last_known_positions[1],
                last_known_positions[2],
                last_known_positions[3],
                last_known_positions[4]
            ])
            transformation_matrix = create_transformation_matrix(src_points, dst_points)
            transformed_frame = cv2.warpPerspective(frame, transformation_matrix, (width, height))
            cv2.imshow("frame", transformed_frame)
            break
        else:
            if check_again >= 30 :
                if last_known_positions[1] is None and not motor0_moved:
                    while time0 < 100:
                        ser.write(f"cal 0 down\n".encode())
                        time0 += 1
                    motor0_moved = True
                if last_known_positions[4] is None and not motor0_moved:
                    while time0 < 100:
                        ser.write(f"cal 0 up\n".encode())
                        time0 += 1
                    motor0_moved = True
                if last_known_positions[3] is None and not motor1_moved:
                    while time1 < 100:
                        ser.write(f"cal 1 down\n".encode())
                        time1 += 1
                    motor1_moved = True
                if last_known_positions[2] is None and not motor1_moved:
                    while time1 < 100:
                        ser.write(f"cal 1 up\n".encode())
                        time1 += 1
                    motor1_moved = True
            check_again += 1

        cv2.imshow("Original", frame)
        if cv2.waitKey(1) & 0xFF == ord('q'):
            break
    if cv2.getWindowProperty('Original', cv2.WND_PROP_VISIBLE) >= 1:
        cv2.destroyAllWindows()
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

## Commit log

2024-05-13 Add files via upload
    Test print for Jonathan to start - thanks!
2024-05-15 add code to control motor with potentiometer
2024-05-16 buttons screens motors integrated
2024-05-20 add calibration
    Add calibration with data from the CV.
    We only calibrate motor0 for now, and we will to extract to which motor the data from CV is for
2024-05-20 Update calibration
    Enhance calibration with CV
2024-05-27 Making the power supply working
2024-05-27 Start adding wiring
2024-05-28 Update README.md with more wiring
2024-05-29 add small bom
2024-05-30 fixed automated player not moving
    [gameplay.ino]
2024-05-30 potentiometer case 3d file
    [potentiometer case.f3d]
2024-05-30 bouncy walls
    [bouncy_walls.3mf]
2024-05-31 adding cad files
    [bottom hemi.stl, bottom_plate.dxf, bouncy_walls.3mf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]
2024-05-31 updating 3d files
    [bottom hemi.stl, bottom_plate.dxf, bouncy_wall_liner.3mf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]
2024-05-31 increase calibration speed and correct light win side
    [gameplay.ino]
